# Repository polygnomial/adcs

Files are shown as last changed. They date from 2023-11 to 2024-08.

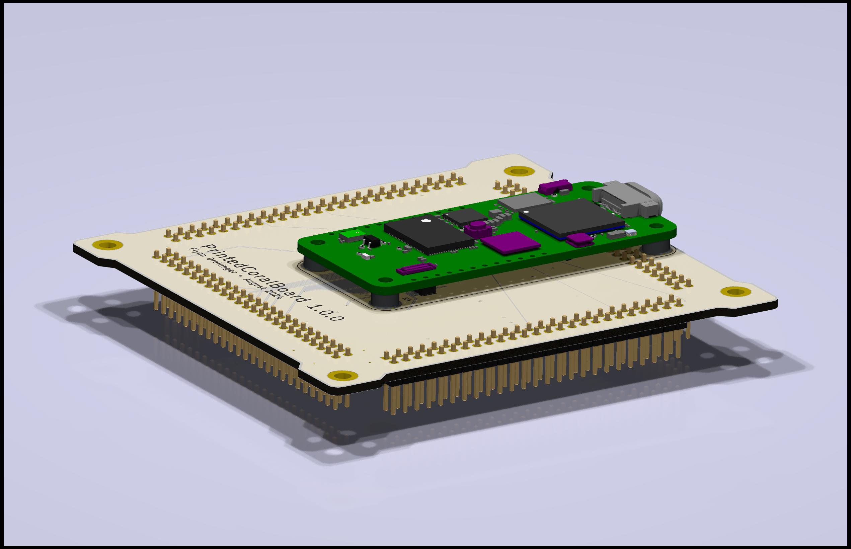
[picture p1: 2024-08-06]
hardware/coral_breakout_board/PrintedCoralBoard1.jpg

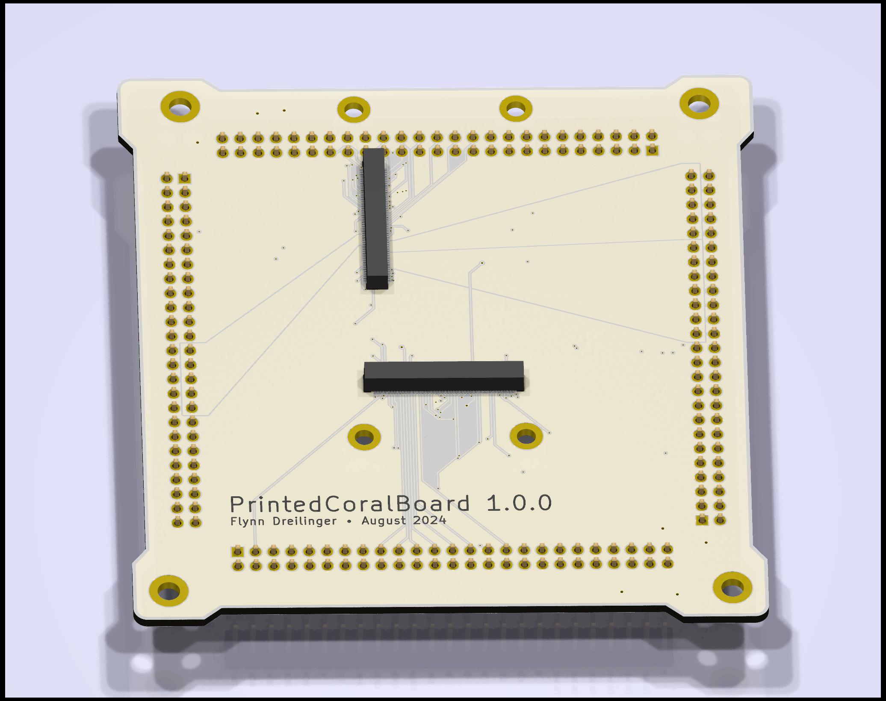
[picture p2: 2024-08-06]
hardware/coral_breakout_board/PrintedCoralBoard.jpg

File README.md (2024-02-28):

# ADCS

## Docs

- Power Architecture
- RT1170 and RT1060 pin map
- slides and other notes
- Tim's review
- TODO move other notes here

## Hardware

### Soldermander

CPU (RT1170) + RAM (MRAM - SEMC and xSPI) + power breakout board, with 2x 100-pin board to board connectors.

### Sqrt of G

Eventual functional ADCS controller and sensor mainboard that the CPU board will sit on top of

### PCBranch

Development breakout board that breaks out all the pins of the RT1170 CPU

---

## Code

### flight

Rust code with a Teensy target, RT1170 target (not yet implemented), etc.

### cpp-code

Useful for checking that I implemented my Rust drivers correctly

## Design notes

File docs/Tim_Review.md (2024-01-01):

- What is the input voltage range? Should annotate that on schematic (voltage min/max, current rating
-- added
- Inductor in line of power input?
-- done, not sure if its the best choice
- "If it's latched up, it won't be executing any code." -Pete 
	- This is not true. A latch up does not necessarily cause the CPU has crashed. In fact it generally does not, and a software protection that detects increased current and power cycles the chip is totally valid.
	- If you want to actually do this, you should do some analysis of the timing. A common way to do this is to have a capacitor on the enable pin, with a weak pull-up, and then an N-FET to ground. When you turn on the GPIO, it turns on the FET, which drains the cap really fast (nanoseconds). It take microseconds to re-charge, giving the power rails time to turn fully off, and giving the latch-up a chance to clear

- You should break out all the GPIO, even the ones the teensy does not. Just leave them as test points.
-- yeah gonna do that
- These too (the ones not going to the JTAG header):
	 ![[Pasted image 20231021010133.png|300]]
- I would add test points to the SD card interface to help debug/software
- SENSORS
	- You should have a power switch to power cycle the sensors. I would say you should put two of each sensor, and have two I2C busses, each with one of each sensor.
	- I2C isolation is not actually super practical, imo. The bus is too complicated to be able to guarantee two devices are isolated. I'd just aim for reliability by redundancy.
	-- will do both, eventually. For now, just multiple devices
	- You should break out more pins of the GPS. At least the PPS pin, which you might want to use. 
	-- added a note to schematic, not gonna do for now
	- What's the deal with this splitter thing? Why not just a splitter, or two GPS's? seems like extra points of failure on zero fault tolerant system.
	-- resolved this

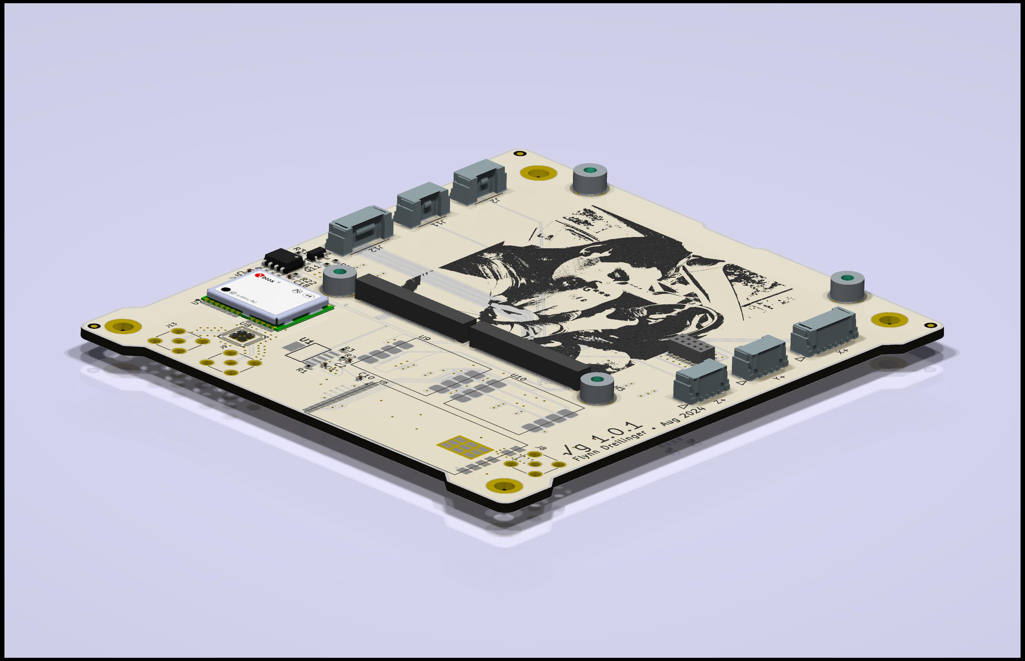
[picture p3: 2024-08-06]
hardware/adcs_with_cpu_board/sqrt_of_g_temp1.jpg

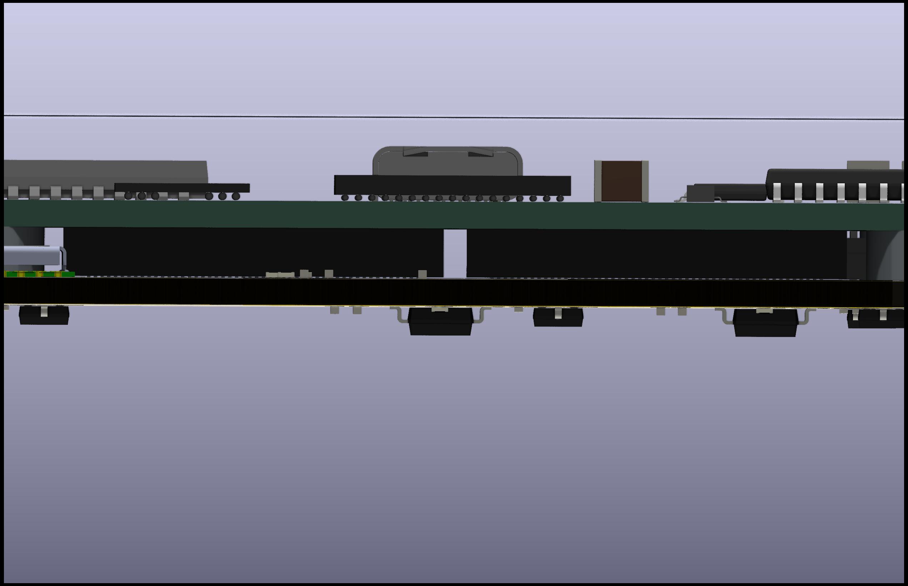
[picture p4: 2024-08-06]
hardware/adcs_with_coral/sqrt_of_g4.jpg

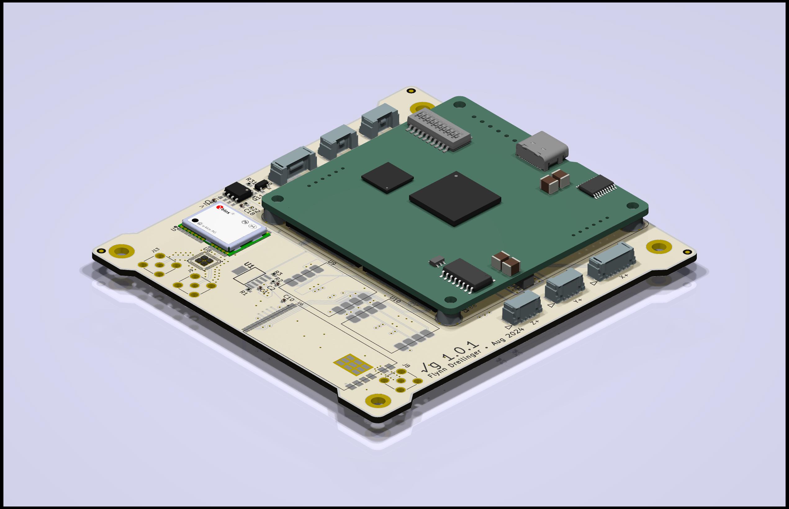
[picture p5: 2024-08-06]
hardware/adcs_with_coral/sqrt_of_g2.jpg

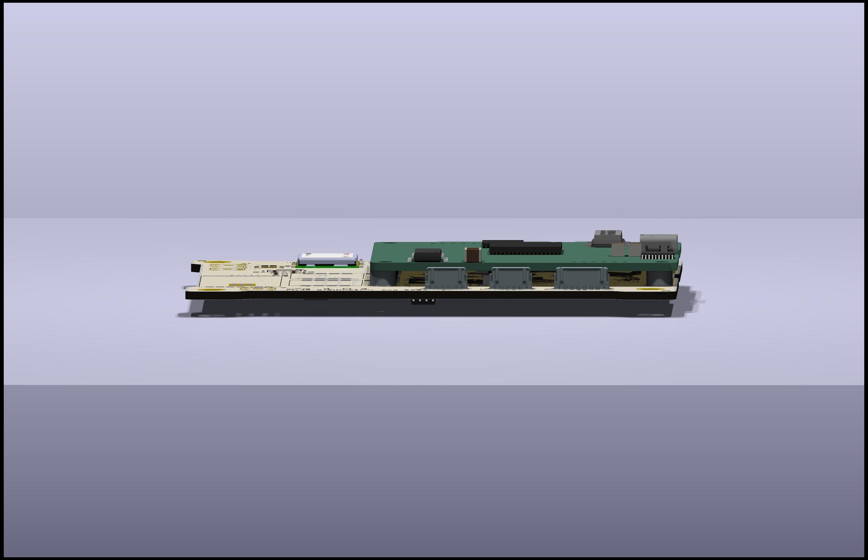
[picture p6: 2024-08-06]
hardware/adcs_with_cpu_board/sqrt_of_g3.jpg

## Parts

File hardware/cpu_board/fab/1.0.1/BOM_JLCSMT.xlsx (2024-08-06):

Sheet: Sheet1
Comment | Designator | Footprint | JLCPCB Part #（optional）
0.1uF | C10, C25, C28, C31, C34, C69, C70, C71, C72, C73, C74, C75, C84, C85 | 402
1uF | C1, C2, C3, C38, C41, C58, C59, C60, C61, C62, C63, C88, C89 | 402
4.7uF | C6, C7, C9, C23, C24, C43, C44, C51, C52, C66, C68 | 402
22uF | C4, C16, C27, C67, C76, C77, C78, C80 | 603
2.2uF | C8, C40, C45, C46, C47, C48, C49, C50 | 402
100uF | C79, C81, C82, C83 | 1210
10pF | C5, C20, C21 | 402
0.22uF | C14, C29 | 402
8pF | C18, C19 | 402
3.3nF | C86, C87 | 402
22nF | C11 | 402
47kΩ | R37, R38, R39, R40, R41, R42, R43, R44, R45, R46, R47, R48 | 402
22kΩ | R51, R52, R53, R54, R55, R56, R57, R58, R59, R60, R61, R62 | 402
10kΩ | R3, R4, R7, R12, R16, R17, R21, R33 | 402 | C3152014,
100kΩ | R8, R15, R19, R24, R31, R32, R49, R50 | 402
4.7kΩ | R9, R10, R63, R64 | 402
0Ω | R2, R26 | 402
30kΩ | R11, R34 | 402
33k | R18, R20 | 402
5.1kΩ | R22, R23 | 402
22.1kΩ | R29, R30 | 402
10mΩ | R1 | R_0402_1005Metric | C5116354
2.2MΩ | R5 | 402
1.27MΩ | R6 | 402
806kΩ | R14 | R_0402_1005Metric | C3016043
4.7K - DNP | R25 | 402
30.1kΩ | R27 | R_0402_1005Metric | C208856
73.2kΩ | R28 | 402
18kΩ | R35 | 402
3.3uH | L3, L4 | L_1210_3225Metric
330uH | L1 | IND_SRN6045TA-331K | C2049953
DLW21HN900SQ2L | L2 | IND4_CHOKE_0805 | C80529
4.7µH | L5 | IND_4x4mm | C5127393
TPS54226PWPRPWP14_2P31X2P46-L | U7, U8 | PWP14_2P31X2P46-L | C72066
TPS16630PWPR | U1 | HTSSOP20_PWP_TEX | C1849462
MIMXRT1176 | U2 | U_MIMXRT1176DVMAA_NXP | C1020268
MT29F1G01ABBFDWB | U4 | UDFN800X600X65-8 | C5330479
USBLC6-2SC6 | U5 | SOT23-6L_STM | C2687116
MT48H32M16LFB4-6 | U6 | VFBGA54_8X8_MRN | C1351581
LT3014IS5-TRMPBF | U9 | S_5_ADI | C666272
CD40109BQNSRQ1 | U10 | NS16 | C2677390
24.0mHz | Y2 | Crystal_SMD_2016-4Pin_2.0x1.6mm | C1986107
32.768kHz | Y3 | Crystal_SMD_3215-2Pin_3.2x1.5mm | C145140
SW_DIP_x10 | SW2 | SW-SMD_DSHP10TS-S | C319046
SW_DIP_x04 | SW3 | SW-SMD_8P-L6.7-W5.4-P1.27-LS8.5 | C319050
190mΩ | FB1, FB2, FB6 | Fuse_0402_1005Metric | C85812
DF40C-100DP-0.4V(51) | J6, J7 | DF40C100DP04V51 | C531031
USB_C_pycubed | J1 | USB_C_Receptacle_XKB_U262-161N-4BVC11 | C319148
JTAG_SWD_10 | J3 | PinHeader_2x05_P1.27mm_Vertical_SMD | C180221

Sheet: Sheet2
References | Value | Footprint | Description | Flight | JLCPCB P/N | Footprint (for JLCPCB) | Power Rating | Voltage Rating | Quantity
C10, C25, C28, C31, C34, C69, C70, C71, C72, C73, C74, C75, C84, C85 | 0.1uF | C_0402_1005Metric |  |  |  |  |  | 10V, 50V | 14
C1, C2, C3, C38, C41, C58, C59, C60, C61, C62, C63, C88, C89 | 1uF | C_0402_1005Metric |  |  |  | 402 |  | 50V, 10V | 13
C6, C7, C9, C23, C24, C43, C44, C51, C52, C66, C68 | 4.7uF | C_0402_1005Metric |  |  |  | 402 |  | 6.3V, 10V | 11
C4, C16, C27, C67, C76, C77, C78, C80 | 22uF | C_0603_1608Metric |  |  |  | 603 |  | 6.3V | 8
C8, C40, C45, C46, C47, C48, C49, C50 | 2.2uF | C_0402_1005Metric |  |  |  | 402 |  | 10V | 8
C79, C81, C82, C83 | 100uF | C_1210_3225Metric | 100uF 16V X5R 1210 |  |  | 1210 |  | 50V | 4
C5, C20, C21 | 10pF | C_0402_1005Metric |  |  |  | 402 |  | 50V | 3
C14, C29 | 0.22uF | C_0402_1005Metric |  |  |  | 402 |  | 50V, 6.3V | 2
C18, C19 | 8pF | C_0402_1005Metric |  |  |  | 402 |  | 50V | 2
C86, C87 | 3.3nF | C_0402_1005Metric | 3.3nF +-10% 100V X7R 0603 |  |  | 402 |  | 50V | 2
C11 | 22nF | C_0402_1005Metric |  |  |  | 402 |  | 50V | 1
R37, R38, R39, R40, R41, R42, R43, R44, R45, R46, R47, R48 | 47kΩ | R_0402_1005Metric |  |  |  | 402 |  |  | 12
R51, R52, R53, R54, R55, R56, R57, R58, R59, R60, R61, R62 | 22kΩ | R_0402_1005Metric |  |  |  | 402 |  |  | 12
R3, R4, R7, R12, R16, R17, R21, R33 | 10kΩ | R_0402_1005Metric |  |  | C3152014, | 402 |  |  | 8
R8, R15, R19, R24, R31, R32, R49, R50 | 100kΩ | R_0402_1005Metric |  |  |  | 402 |  |  | 8
R9, R10, R63, R64 | 4.7kΩ | R_0402_1005Metric |  |  |  | 402 |  |  | 4
R2, R26 | 0Ω | R_0402_1005Metric |  |  |  | 402 |  |  | 2
R11, R34 | 30kΩ | R_0402_1005Metric |  |  |  | 402 |  |  | 2
R18, R20 | 33k | R_0402_1005Metric |  |  |  | 402 |  |  | 2
R22, R23 | 5.1kΩ | R_0402_1005Metric | 5.1k 0402 |  |  | 402 |  |  | 2
R29, R30 | 22.1kΩ | R_0402_1005Metric | 22.1K 0402 |  |  | 402 |  |  | 2
R1 | 10mΩ | R_2512_6332Metric |  |  | C5116354 | 2512 | 3W |  | 1
R5 | 2.2MΩ | R_0402_1005Metric |  |  |  | 402 |  |  | 1
R6 | 1.27MΩ | R_0402_1005Metric |  |  |  | 402 |  |  | 1
R14 | 806kΩ | R_0402_1005Metric |  |  | C3016043 | 402 |  |  | 1
R25 | 4.7K - DNP | R_0402_1005Metric |  |  |  | 402 |  |  | 1
R27 | 30.1kΩ | R_0402_1005Metric | 30.1K 0402 |  | C208856 | 402 |  |  | 1
R28 | 73.2kΩ | R_0402_1005Metric | 73.2K 0402 |  |  | 402 |  |  | 1
R35 | 18kΩ | R_0402_1005Metric |  |  |  | 402 |  |  | 1
L3, L4 | 3.3uH | L_1210_3225Metric | 3.3uH Shielded Inductor | SRP3212-3R3M |  |  | 3.1A, 3.4A Saturation |  | 2
L1 | 330uH | IND_SRN6045TA-331K | Inductor | SRN6045TA-331K | C2049953 |  |  |  | 1
L2 | DLW21HN900SQ2L | IND4_CHOKE_0805 | Inductor | DLW21HN900SQ2L | C80529 |  |  |  | 1
L5 | 4.7µH | IND_4x4mm |  | SNR4030-4R7MT | C5127393 |  |  |  | 1
U7, U8 | TPS54226PWPRPWP14_2P31X2P46-L | PWP14_2P31X2P46-L | Adjustable Switching Regulator | TPS54226PWPR | C72066 |  |  |  | 2
U1 | TPS16630PWPR | HTSSOP20_PWP_TEX | Load Switch | TPS16630PWPR | C1849462 |  |  |  | 1
U2 | MIMXRT1176 | U_MIMXRT1176DVMAA_NXP | Microcontroller | MIMXRT1176AVM8A | C1020268 |  |  |  | 1
U3 | EM064LXQADG13IS1T | SON127P800X600X95-9N-D | STT-MRAM (xSPI) | EM064LXQADG13IS1T |  |  |  |  | 1
U4 | MT29F1G01ABBFDWB | UDFN800X600X65-8 | NAND Flash | MT29F1G01ABBFDWB | C5330479 |  |  |  | 1
U5 | USBLC6-2SC6 | SOT23-6L_STM | USB TVS diodes | USBLC6-2SC6 | C2687116 |  |  |  | 1
U6 | MT48H32M16LFB4-6 | VFBGA54_8X8_MRN | SDRAM | MT48H32M16LFB4-6 | C1351581 |  |  |  | 1
U9 | LT3014IS5-TRMPBF | S_5_ADI | Adjustable LDO |  | C666272 |  |  |  | 1
U10 | CD40109BQNSRQ1 | NS16 | Level Shifter |  | C2677390 |  |  |  | 1
Y2 | 24.0mHz | Crystal_SMD_2016-4Pin_2.0x1.6mm | 24.0mHz Crystal Oscillator | XRCGB24M000F1H01R0 | C1986107 |  |  |  | 1
Y3 | 32.768kHz | Crystal_SMD_3215-2Pin_3.2x1.5mm | 32.768kHz Crystal Oscillator | 20021221-00010C4LF | C145140 |  |  |  | 1
SW1 | SWITCH_SMT4.6X2.8 | BTN_KMR2_4.6X2.8 |  |  |  |  |  |  | 1
SW2 | SW_DIP_x10 | SW-SMD_DSHP10TS-S |  |  | C319046 |  |  |  | 1
SW3 | SW_DIP_x04 | SW-SMD_8P-L6.7-W5.4-P1.27-LS8.5 |  |  | C319050 |  |  |  | 1
FB1, FB2, FB6 | 190mΩ | Fuse_0402_1005Metric | Ferrite Bead | BLM15AG121SN1D | C85812 | 401 |  |  | 3
H2, H3, H4 | MountingHole_Pad | MountingHole_2.7mm_M2.5_DIN965_Pad |  |  |  |  |  |  | 3
J2, J4 | 353620650 | MOLEX_35362-0650 | 6-pin sherlock through-hole connector | 353620650 |  |  |  |  | 2
J6, J7 | DF40C-100DP-0.4V(51) | DF40C100DP04V51 | Hirose Board-to-Board Connector | DF40C-100DP-0.4V(51) | C531031 |  |  |  | 2
J1 | USB_C_pycubed | USB_C_Receptacle_XKB_U262-161N-4BVC11 | USB C Receptacle | U262-161N-4BVC11 | C319148 |  |  |  | 1
J3 | JTAG_SWD_10 | PinHeader_2x05_P1.27mm_Vertical_SMD | JTAG/SWD 10-pin connector | BD125-10-A-0305-0580-L-B | C180221 |  |  |  | 1
J5 | Conn_01x06 | PinHeader_1x06_P2.54mm_Vertical |  |  |  |  |  |  | 1
J8 | SAMTEC-FTS-105-03-X-DV | SAMTEC-FTS-105-03-X-DV |  |  |  |  |  |  | 1

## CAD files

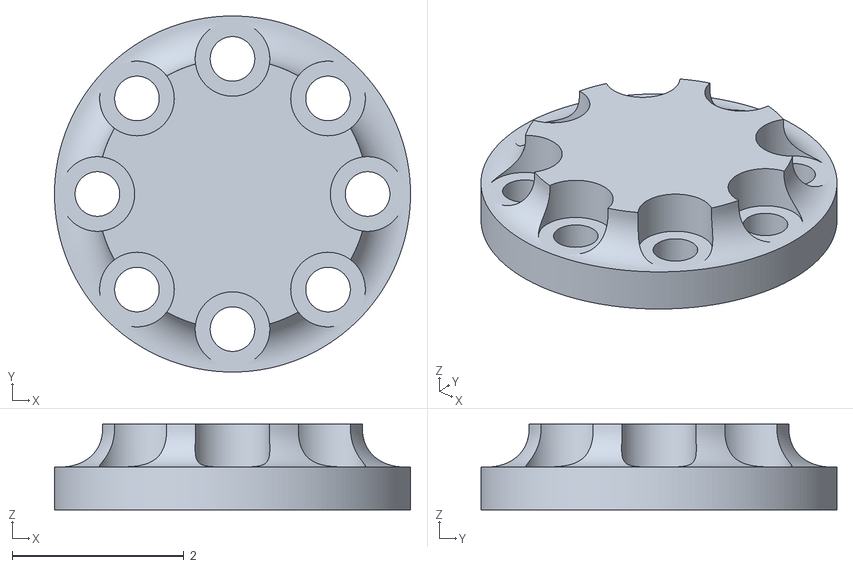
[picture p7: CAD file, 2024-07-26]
calibration/flange_test_mount.stl
4.15 x 4.15 x 1.00

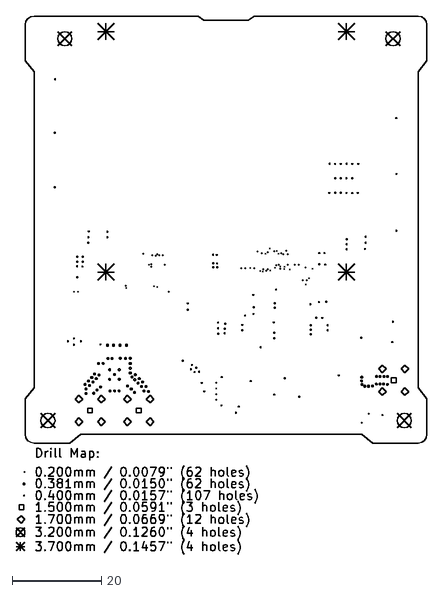
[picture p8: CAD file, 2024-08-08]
hardware/adcs_with_coral/fab/sqrt_of_g-PTH-drl_map.dxf
92.2 x 120.8

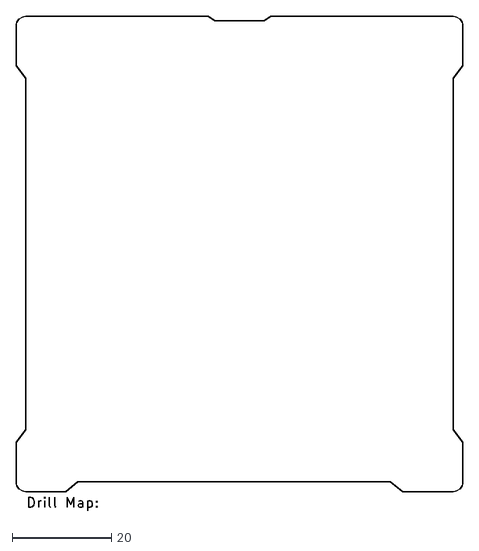
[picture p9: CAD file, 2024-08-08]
hardware/adcs_with_cpu_board/fab/sqrt_of_g-NPTH-drl_map.dxf
90.2 x 99.7

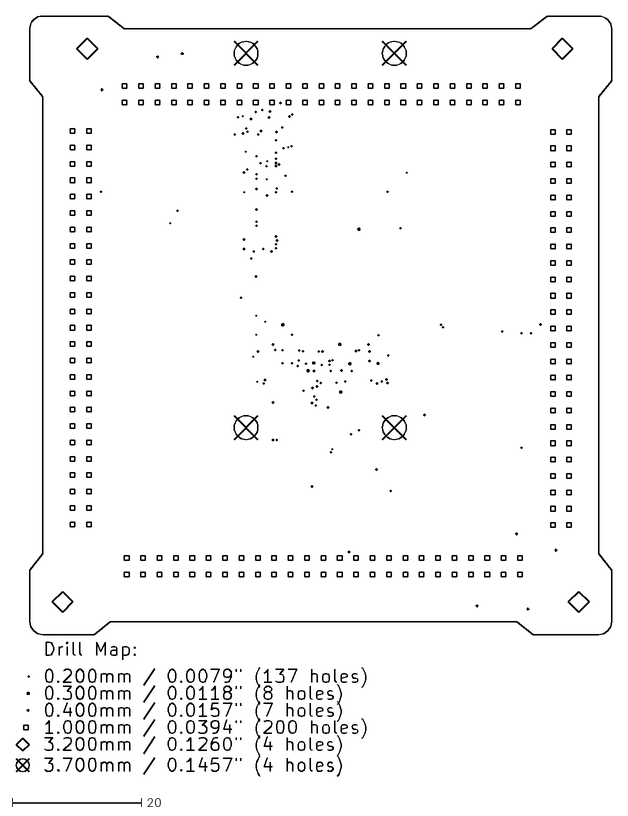
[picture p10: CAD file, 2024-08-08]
hardware/coral_breakout_board/fab/PrintedCoralBoard-PTH-drl_map.dxf
92.2 x 117.8

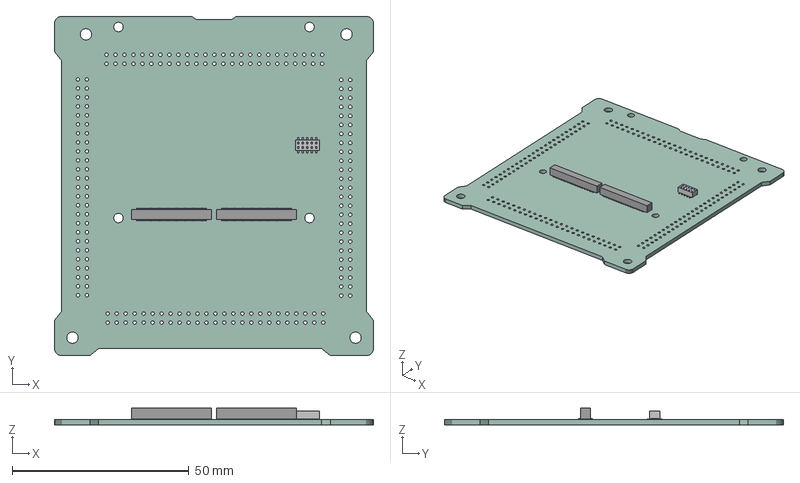
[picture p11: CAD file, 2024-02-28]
hardware/coral_breakout_board/PrintedCoralBoard.step
90.2 x 95.9 x 4.78 mm
_autosave-PCBranch PCB

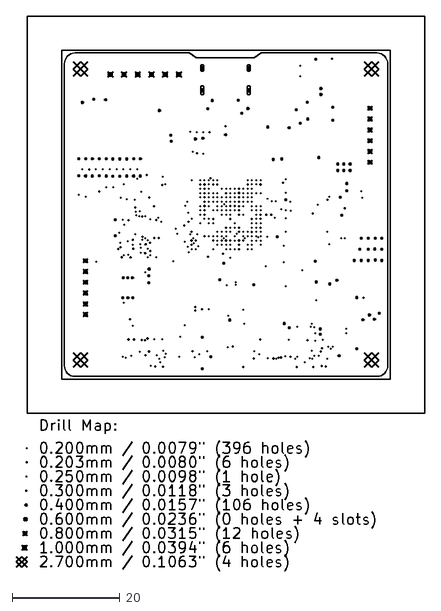
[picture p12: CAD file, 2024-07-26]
hardware/cpu_board/fab/1.0.1/Soldermander_panelized_panelized-PTH-drl_map.dxf
75.8 x 103.0

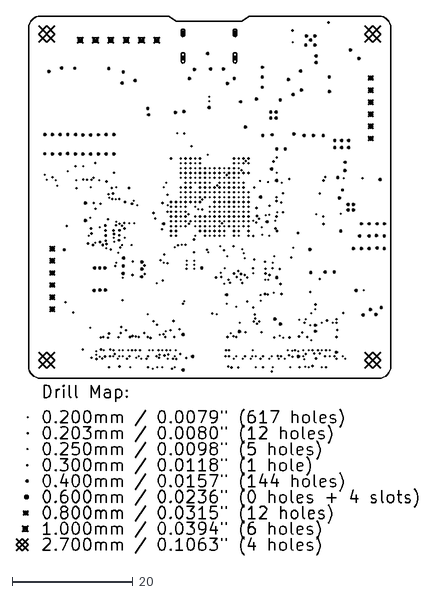
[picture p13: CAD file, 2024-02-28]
hardware/cpu_board/fab/1.0/cpu_board-PTH-drl_map.dxf
66.5 x 89.3

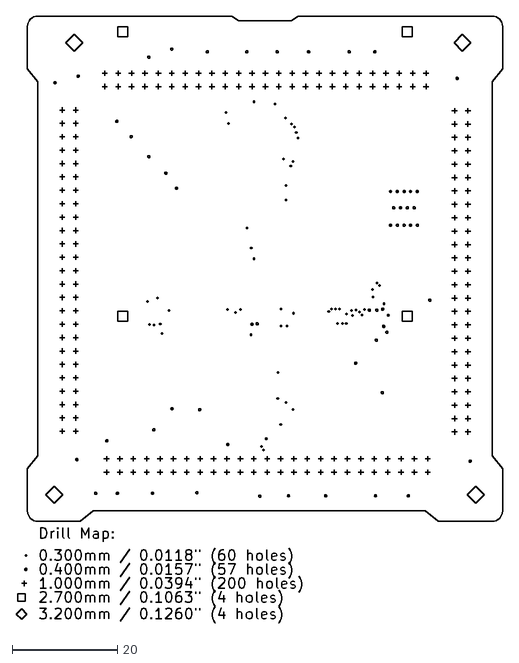
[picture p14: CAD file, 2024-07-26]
hardware/cpu_board_breakout/fab/1.0.1/PCBranch-PTH-drl_map.dxf
92.2 x 115.2

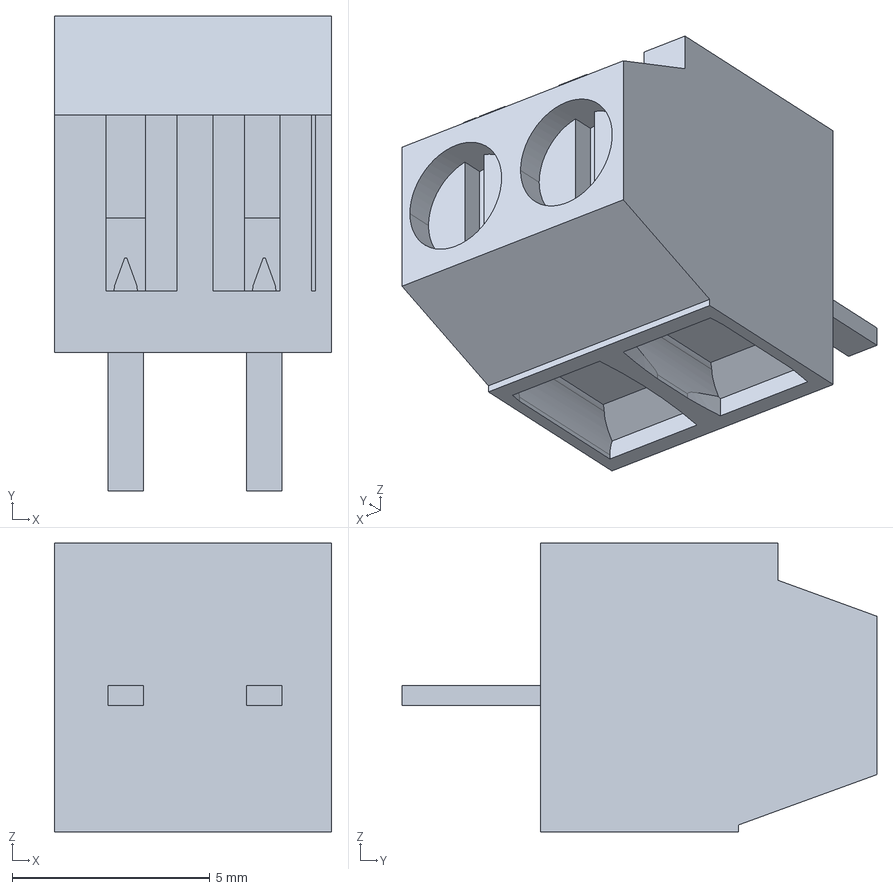
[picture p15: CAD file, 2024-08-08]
hardware/models/c-1776112-2-o-3d.stp
7.00 x 12.0 x 7.30 mm

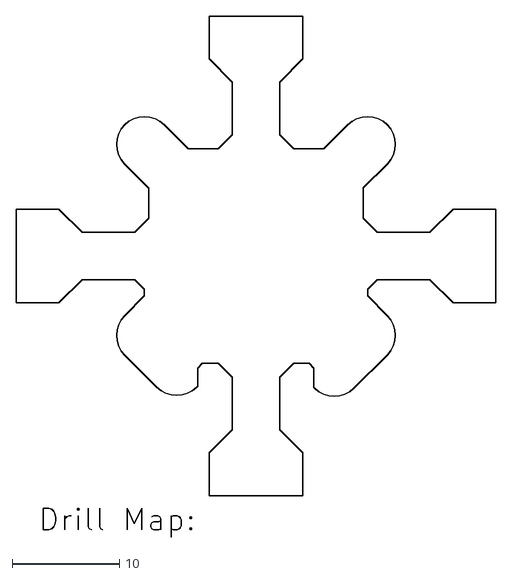
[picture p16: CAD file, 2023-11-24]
hardware/sun_sensor_pyramid/gerbers/sfh2430_breakout-NPTH-drl_map.dxf
44.7 x 48.6

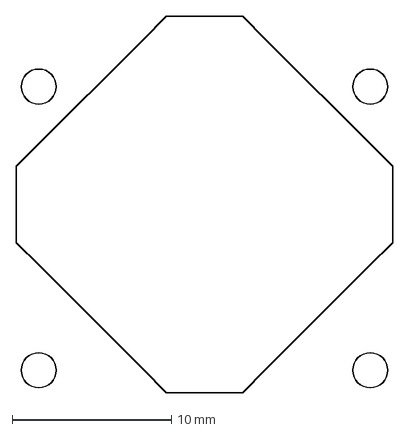
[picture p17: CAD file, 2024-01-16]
hardware/sun_sensor_pyramid/sun pyramid mounting.dxf
23.6 x 23.6 mm

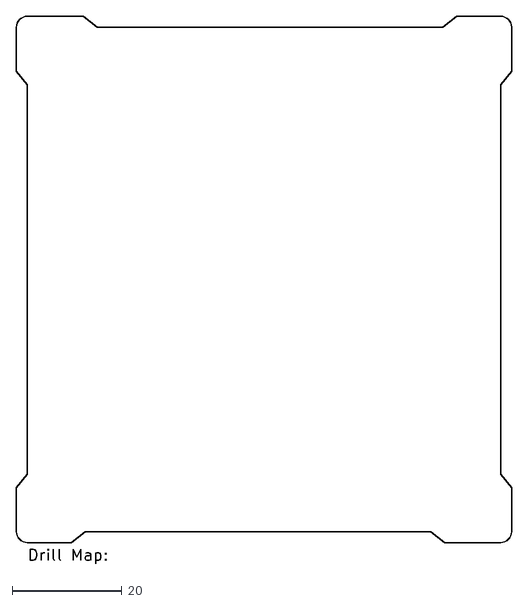
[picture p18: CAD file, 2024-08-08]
hardware/coral_breakout_board/fab/PrintedCoralBoard-NPTH-drl_map.dxf
90.2 x 99.7

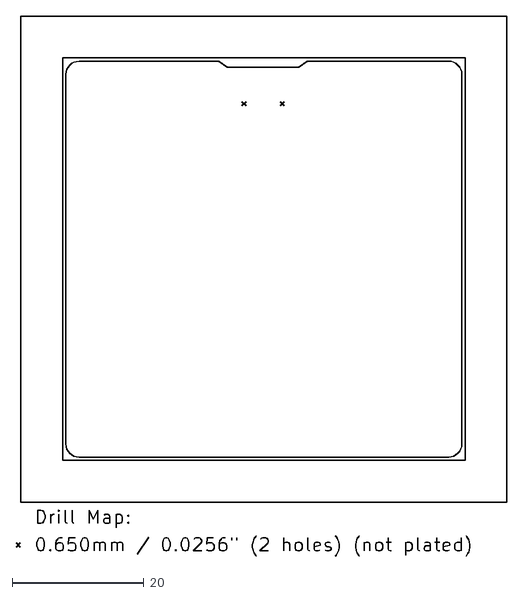
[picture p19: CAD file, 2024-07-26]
hardware/cpu_board/fab/1.0.1/Soldermander_panelized_panelized-NPTH-drl_map.dxf
74.4 x 81.8

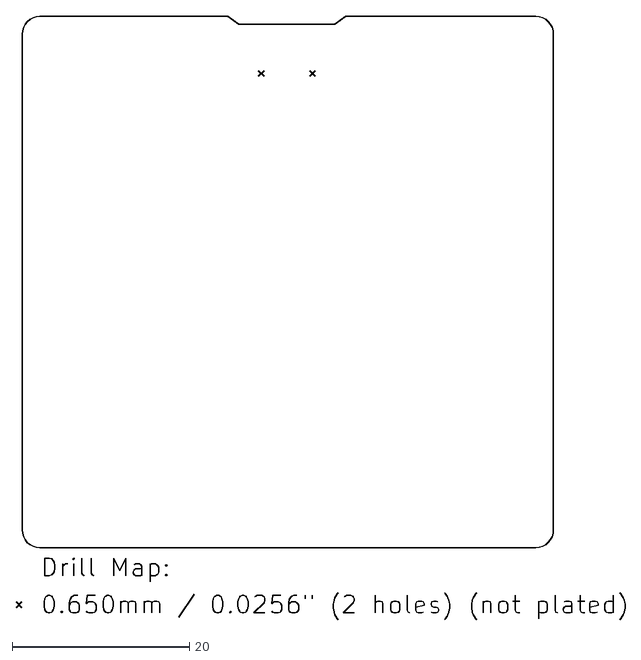
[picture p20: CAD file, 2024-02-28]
hardware/cpu_board/fab/1.0/cpu_board-NPTH-drl_map.dxf
68.8 x 68.1

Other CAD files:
hardware/cpu_board_breakout/fab/1.0.1/PCBranch-NPTH-drl_map.dxf
hardware/models/10DIP.step
hardware/models/2053380006.stp
hardware/models/35362-0850.stp
hardware/models/353621050.stp
hardware/models/5055670631.stp
hardware/models/5055680431.stp
hardware/models/5055680631.stp
hardware/models/9774030151R.stp
hardware/models/BMI270.step
hardware/models/CLP-105-02-F-D.stp
hardware/models/CONN_PH1RB-06.step
hardware/models/DF40HC_3.0_-100DS-0.4V_51_.stp
hardware/models/DRV8332DKDR.stp
hardware/models/EM064LXOAB320IS1T.stp
hardware/models/EM064LXQADG13IS1T.stp
hardware/models/FTS-105-03-F-DV.stp
hardware/models/MIMXRT1062DVJ6B.step
hardware/models/MT29F2G01ABBGDWB-IT_G_TR.stp
hardware/models/NEO.STEP
hardware/models/NS0016A.stp
hardware/models/PWP0020T.stp
hardware/models/RFM95W-915S2.step
hardware/models/SFH_2430-Z.step
hardware/models/SMA-J-P-H-ST-EM1--3DModel-STEP-269445.STEP
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

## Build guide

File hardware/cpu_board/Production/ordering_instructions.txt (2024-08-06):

Ordering Instructions:
Panel dimensions: 73.70 x 73.71 mm.
Solder Mask: Red (Default)
Silkscreen: White (Default)
Layers: 6
Finish: HASL Lead-free (Default)
Thickness: 1.6mm (Default)
Copper weight: 1oz (Default)
Minimum track width: 0.09mm (3.54mil)
Minimum via drill: 0.20mm (7.87mil)

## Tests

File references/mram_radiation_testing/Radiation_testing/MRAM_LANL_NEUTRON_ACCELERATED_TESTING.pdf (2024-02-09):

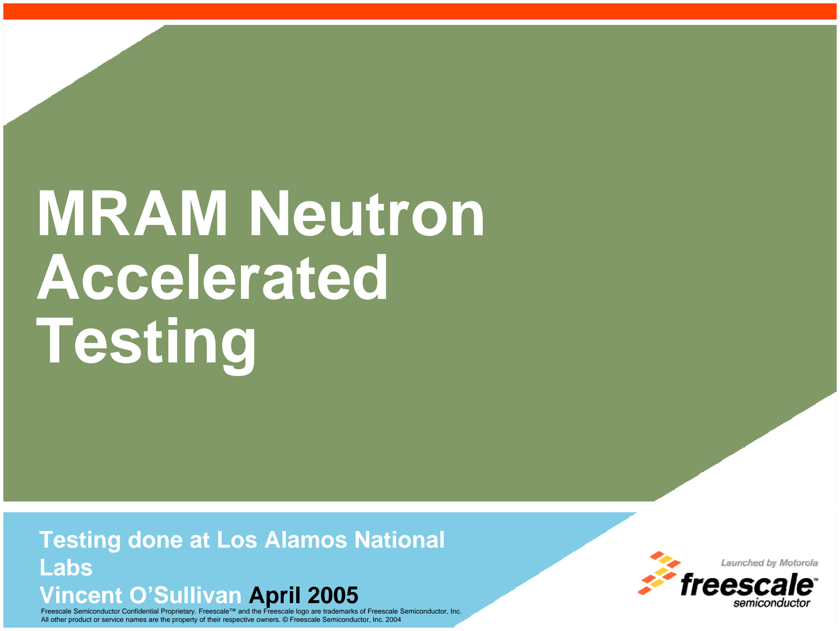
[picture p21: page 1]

Freescale Semiconductor Confidential Proprietary. Freescale™ and the Freescale logo are trademarks of Freescale Semiconductor, Inc. All other product or service names are the property of their respective owners. © Freescale Semiconductor, Inc. 2004

# MRAM Neutron Accelerated Testing

# Testing done at Los Alamos National Labs Vincent O’Sullivan April 2005

## Slide 2

# LANL Neutron Beam Overview

# LANL Neutron Beam at WNR Facilty

# - Intensity: 100M x Ambient Neutron Flux at Sea Level New York City - Energy Spectrum: Approx 1Mev to 800Mev per neutron - Spectrum is close to Ambient Neutron flux from Sea level up to commercial aircraft altitudes

# Ambient Neutron Spectrum vs WNR Spectrum

# Comparison of Neutron Flux at Ground Level and in WNR beam

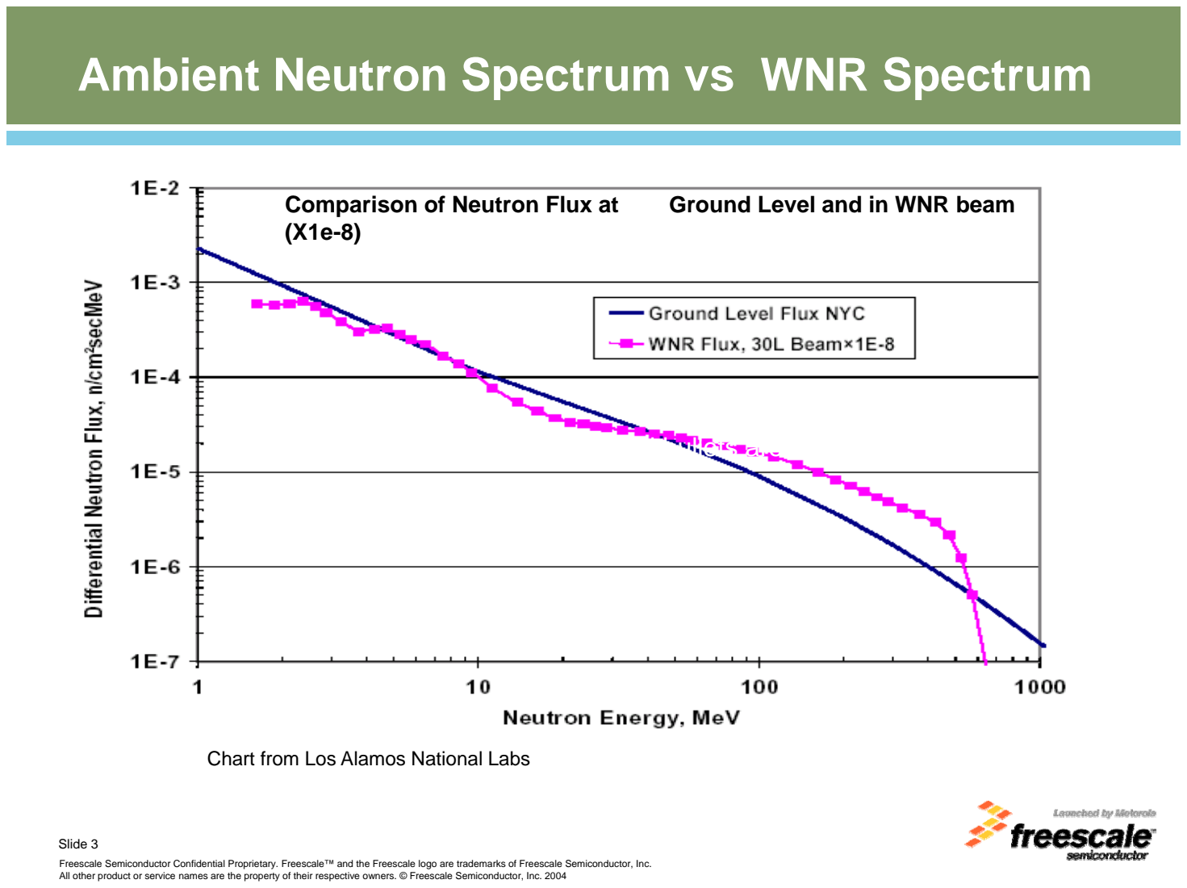
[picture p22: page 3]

## Slide 3

(X1e-8)

# ▪Third and fourth-level bullets are 16 pt Arial

# Chart from Los Alamos National Labs

## Slide 4

# Test Procedure

- Write 8 devices with all ones and 8 devices with all zeroes.

# - Expose sets of 4 devices with both data states to significantly different doses of neutrons

- Maintain 1 set of 4 with both data states as controls.

# - Capture bit fail before and after beam exposure

# - Used devices from Lot T38838

## Slide 5

# Data Summary

Run | | Total Neutrons/cm2 >10Mev | Equivalent Device Hours in NYC | Total bit fails Pre | Total Bit Fails Post
0 | Set 0 | 0 | | 37 | 40
1.0 | Set 1 | 853075578.5 | 60933969.89 | 11 | 3
2.0 | Set 2 | 851959966.4 | 60854283.32 | 8 | 6
3.0 | Set 3
4.0 | Set 3
5.0 | Set 3 | 14142335140 | 1010166796 | 4 | 3
6.0 | Set 4
7.0 | Set 4
8.0 | Set 4
8.1 | Set 4
9.0 | Set 4
10.0 | Set 4
11.0 | Set 4 | 58341176078 | 4167226863 | 0 | 1

# Neutrons are apparently good for MRAM! Worst case

provides a FIT rate of no higher than 4.2. Number of fails,

# however, are too small, and within inherent non

repeatability of setup.

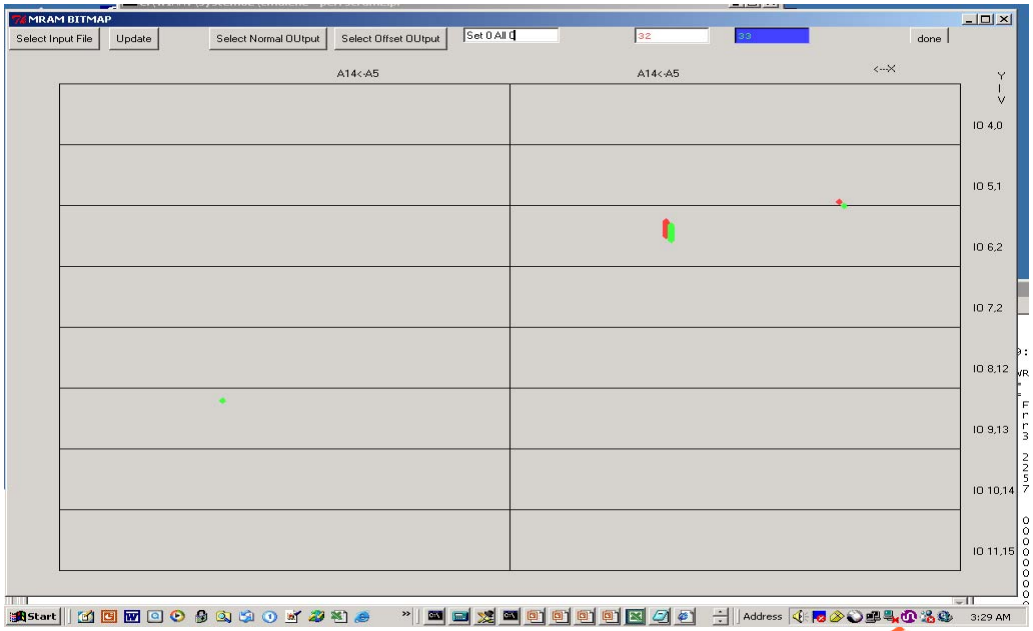
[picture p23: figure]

## Slide 6

# Set0 All 0 Pre Post

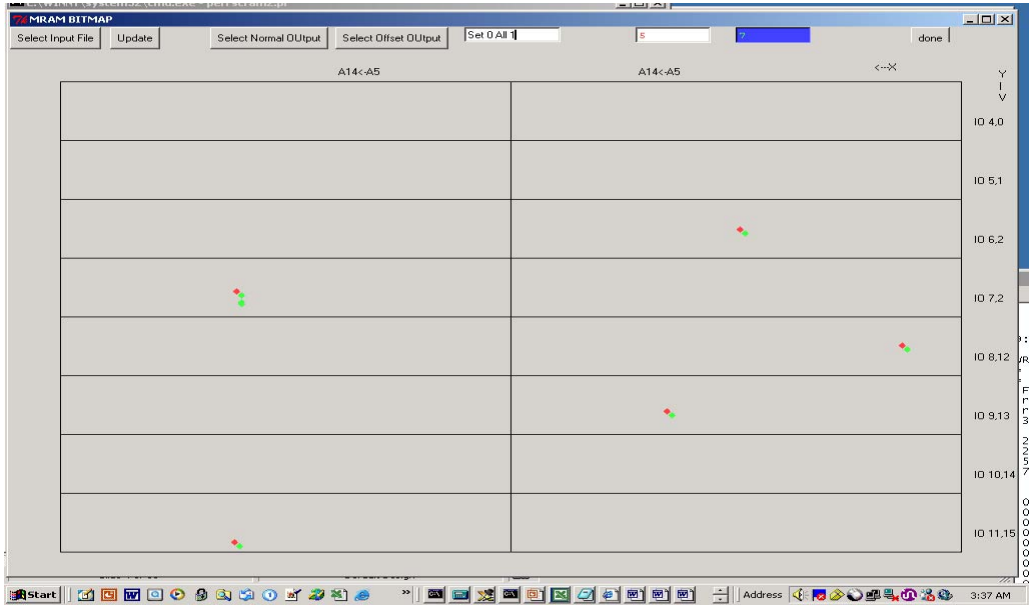
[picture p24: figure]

## Slide 7

# Set0 All 1 Pre Post

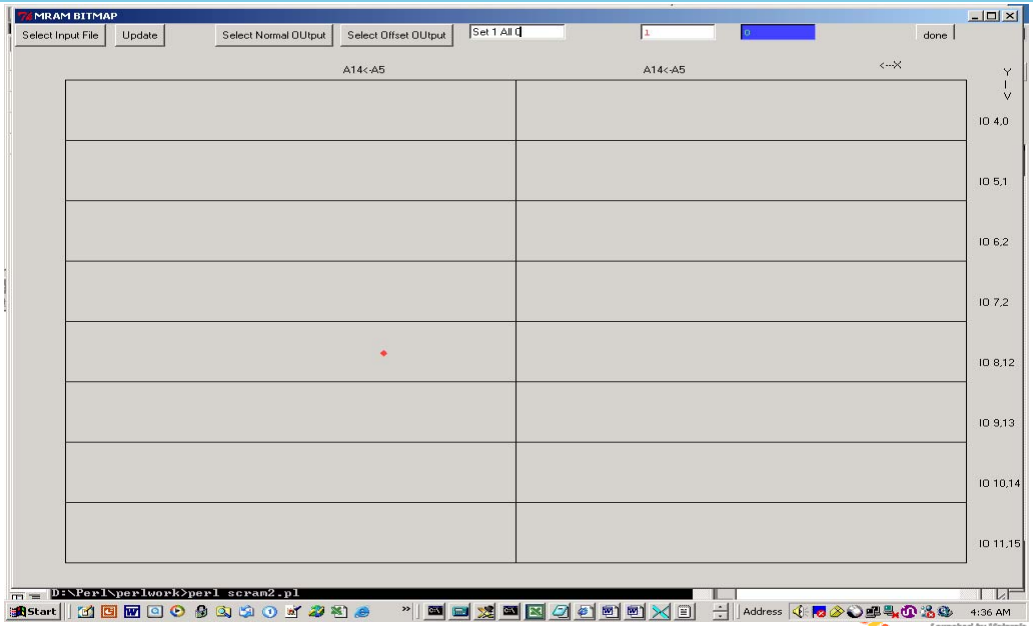
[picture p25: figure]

## Slide 8

# Set1 All 0 Pre Post

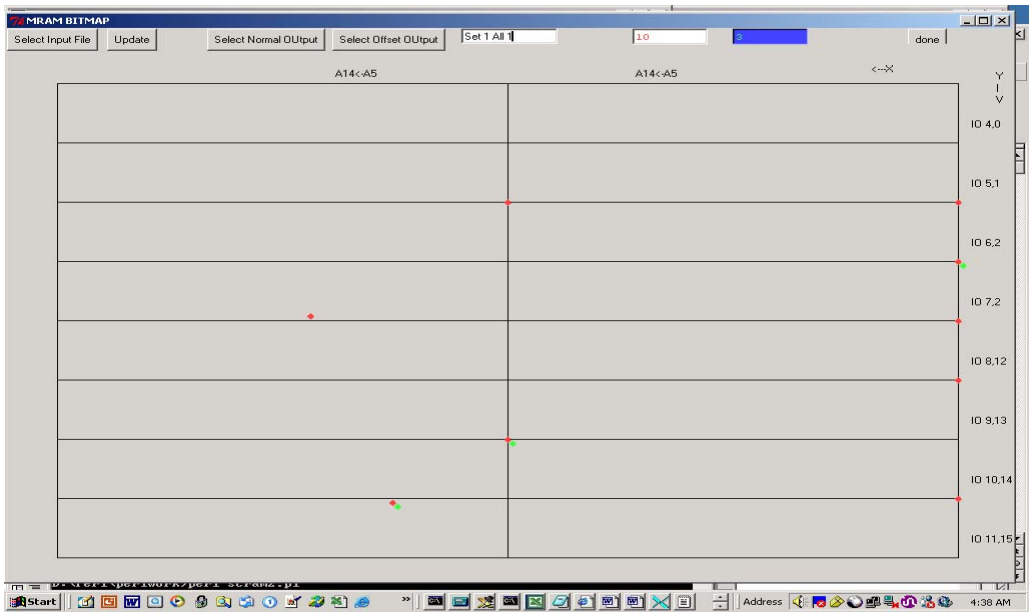
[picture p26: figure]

## Slide 9

# Set1 All 1 Pre Post

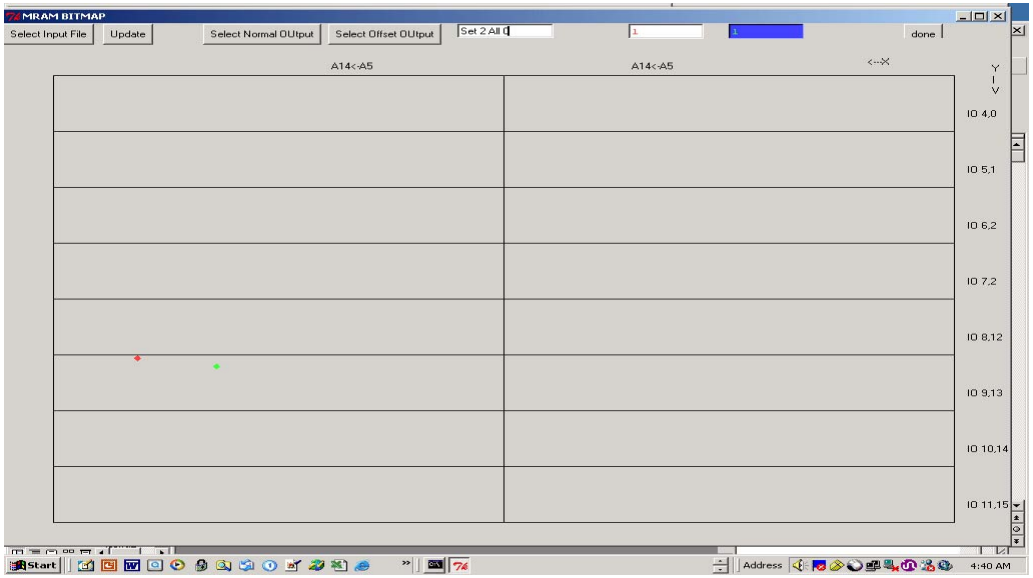
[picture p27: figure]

## Slide 10

# Set 2 All 0 Pre Post

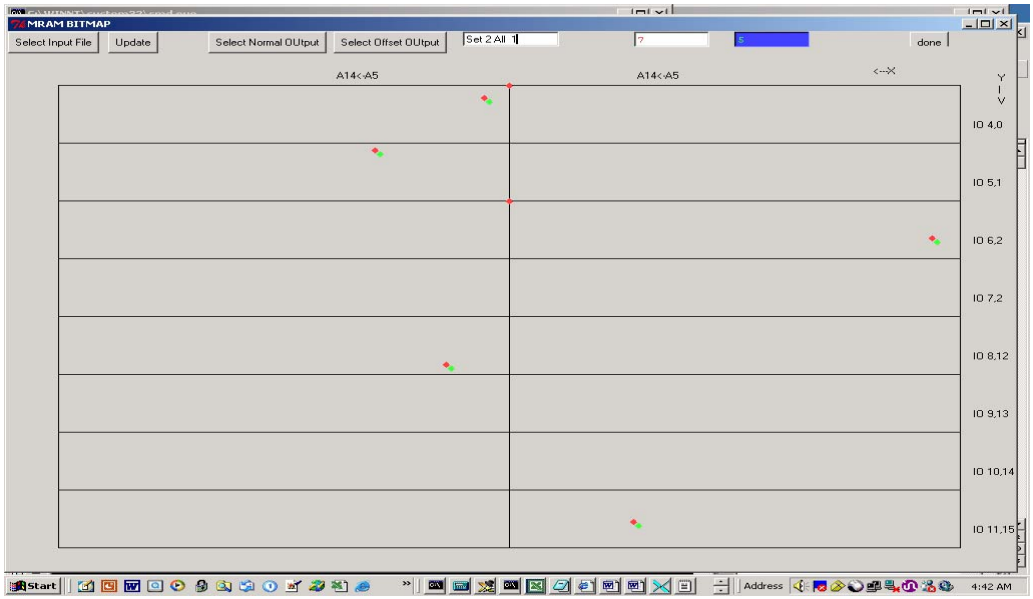
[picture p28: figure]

## Slide 11

# Set 2 All 1 Pre Post

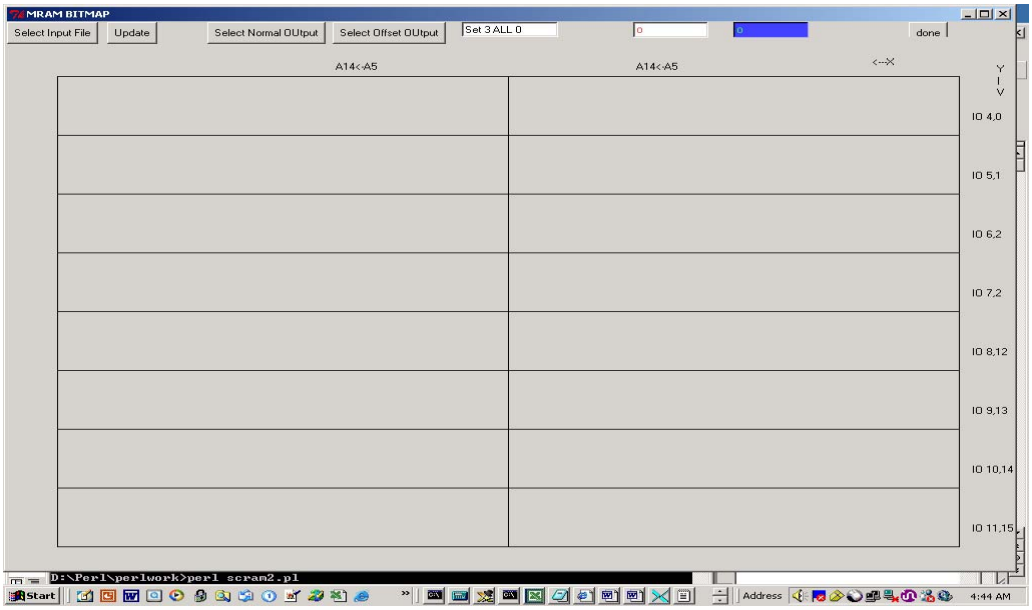
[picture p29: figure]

## Slide 12

# Set 3 All 0 Pre Post

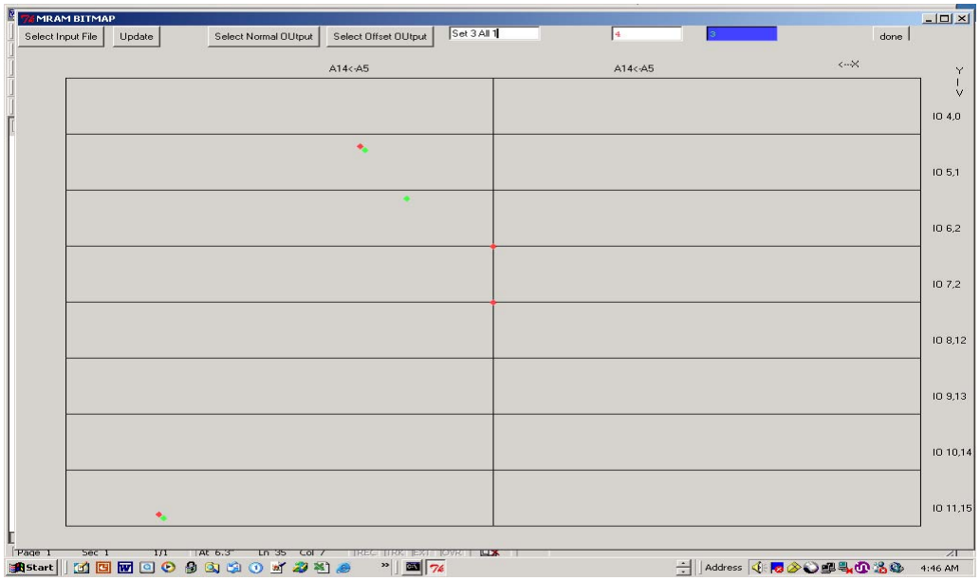
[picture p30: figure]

## Slide 13

# Set 3 All 1 Pre Post


## Slide 14

# Set 4 All 0 Pre Post


## Slide 15

# Set 4 All 1 Pre Post

## Slide 16

# Conclusions

# - MRAM Static SER FIT rate due to neutrons is likely 100’s X less than the latest SRAM technologies - To Do:

# - Characterize dynamic MRAM neutron accelerated SER - If MRAM bitcell proves as robust as expected against neutron accelerated soft error, it may be used to characterize transistor technologies in periphery against neutron accelerated dynamic SER

- MRAM Alpha accelerated soft error needs verification.


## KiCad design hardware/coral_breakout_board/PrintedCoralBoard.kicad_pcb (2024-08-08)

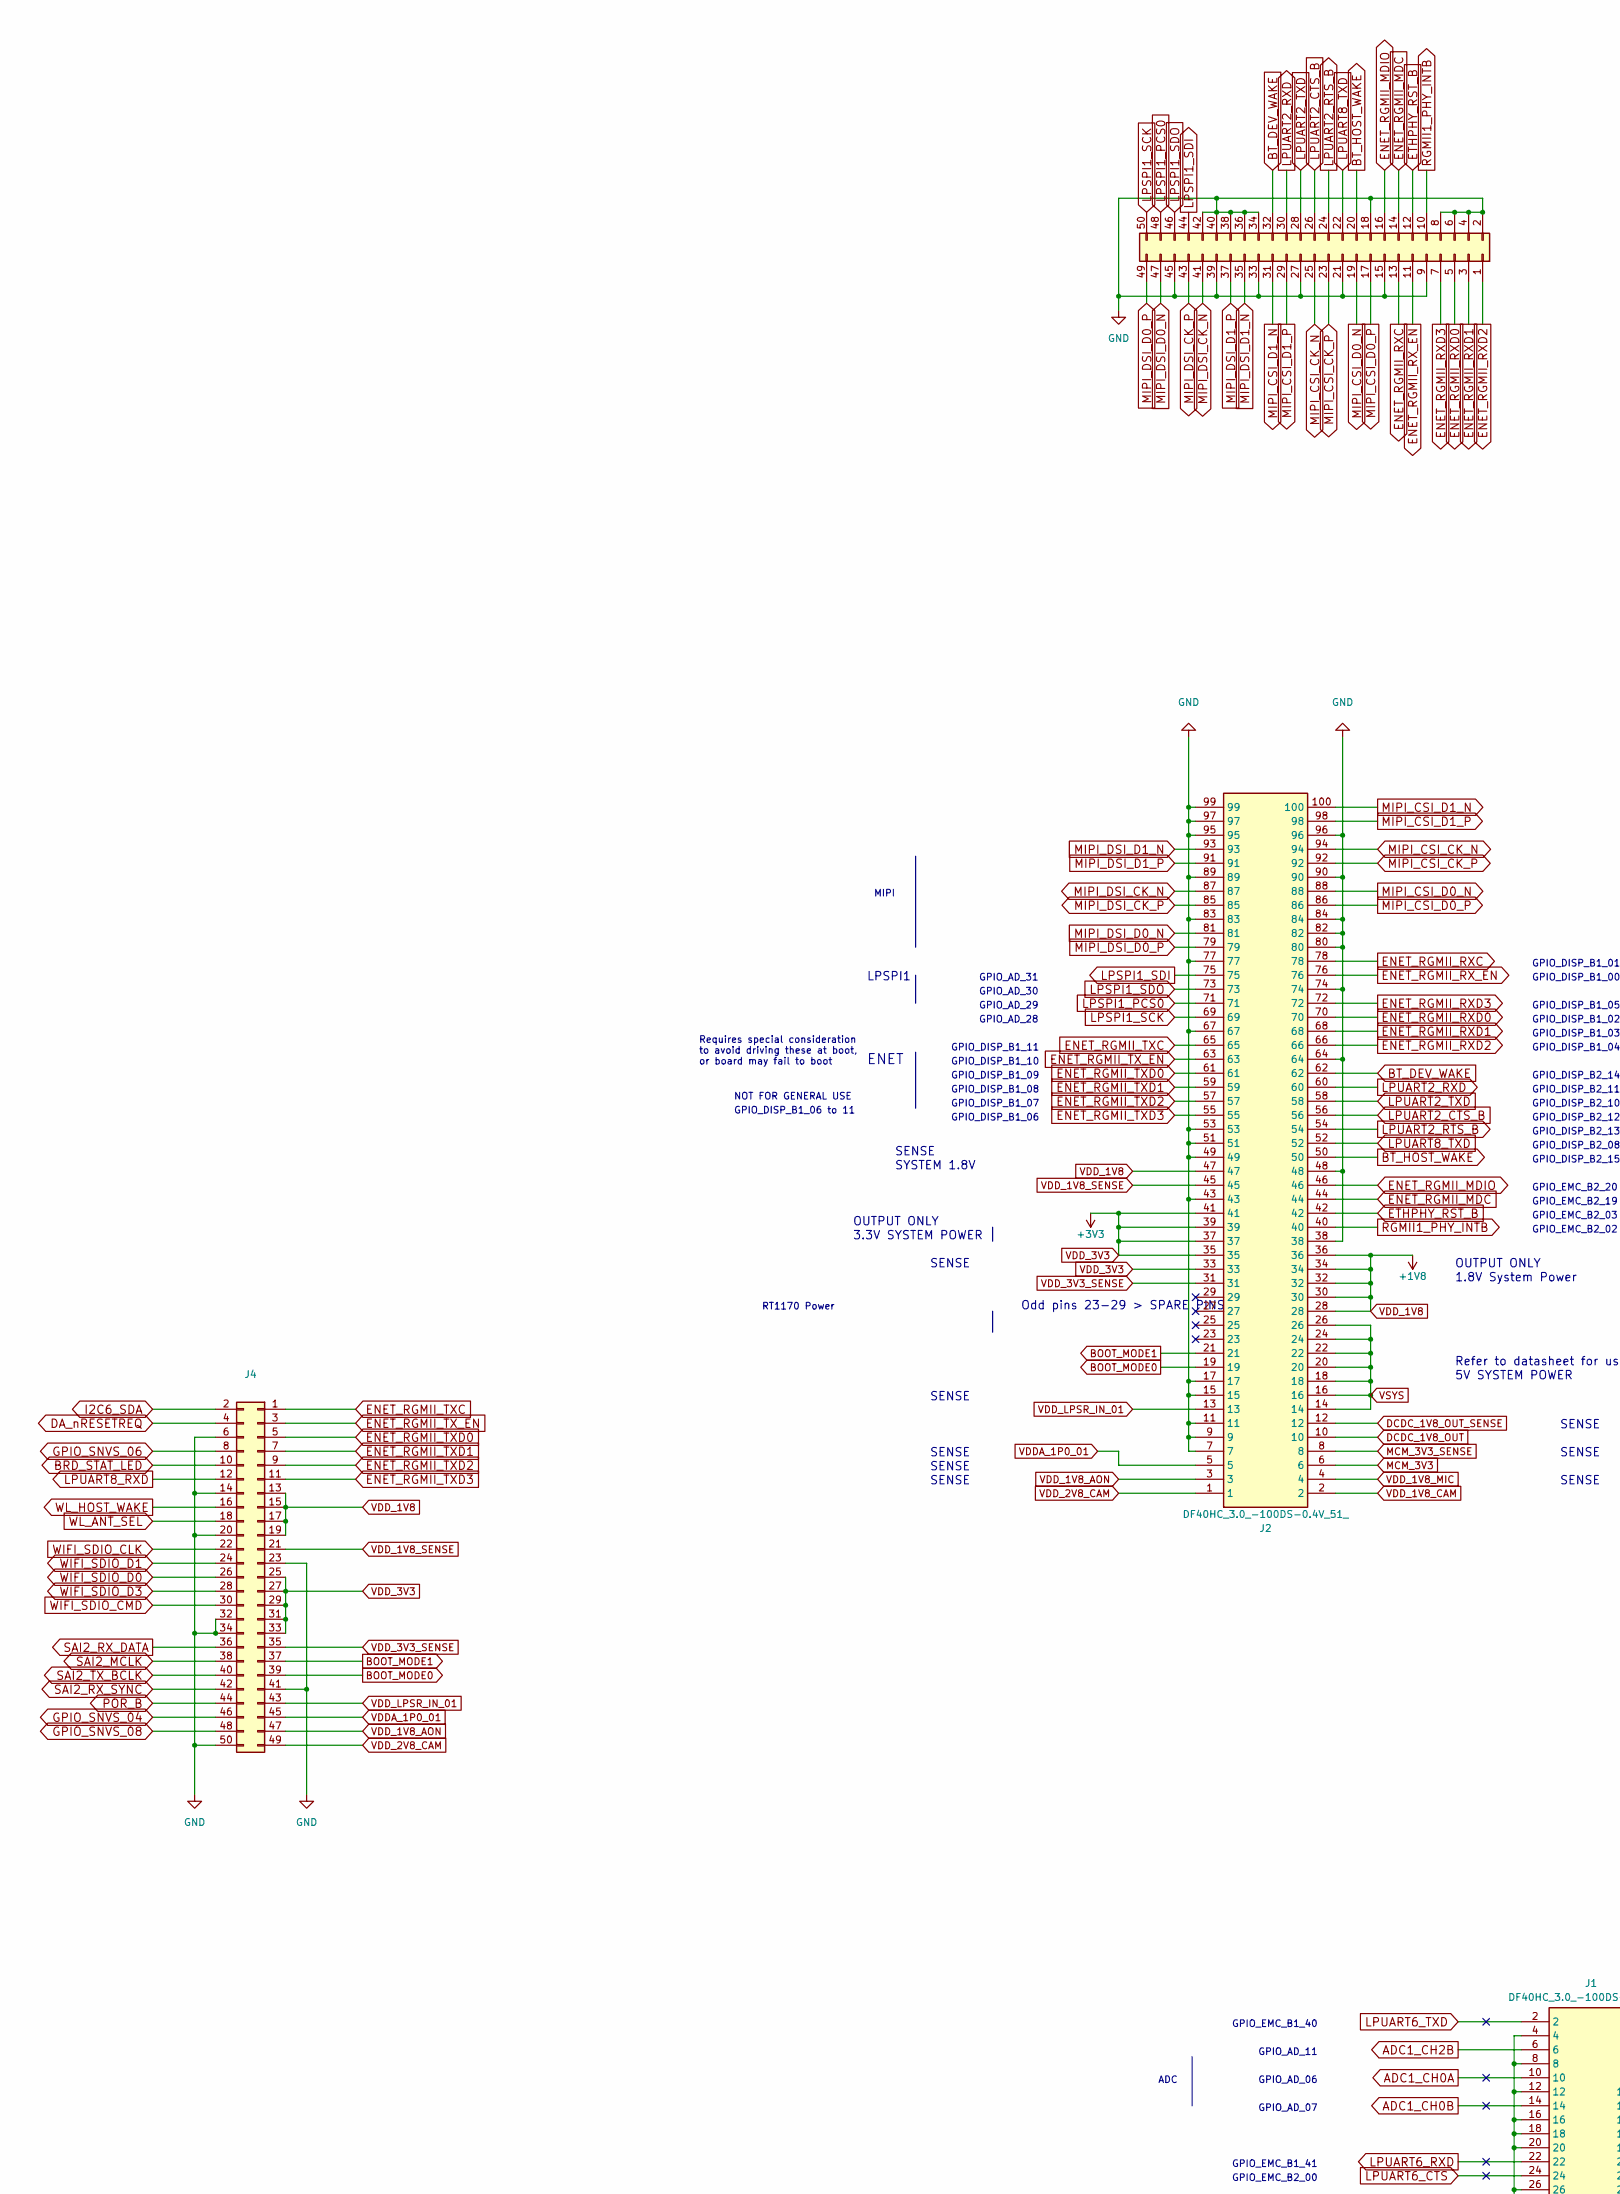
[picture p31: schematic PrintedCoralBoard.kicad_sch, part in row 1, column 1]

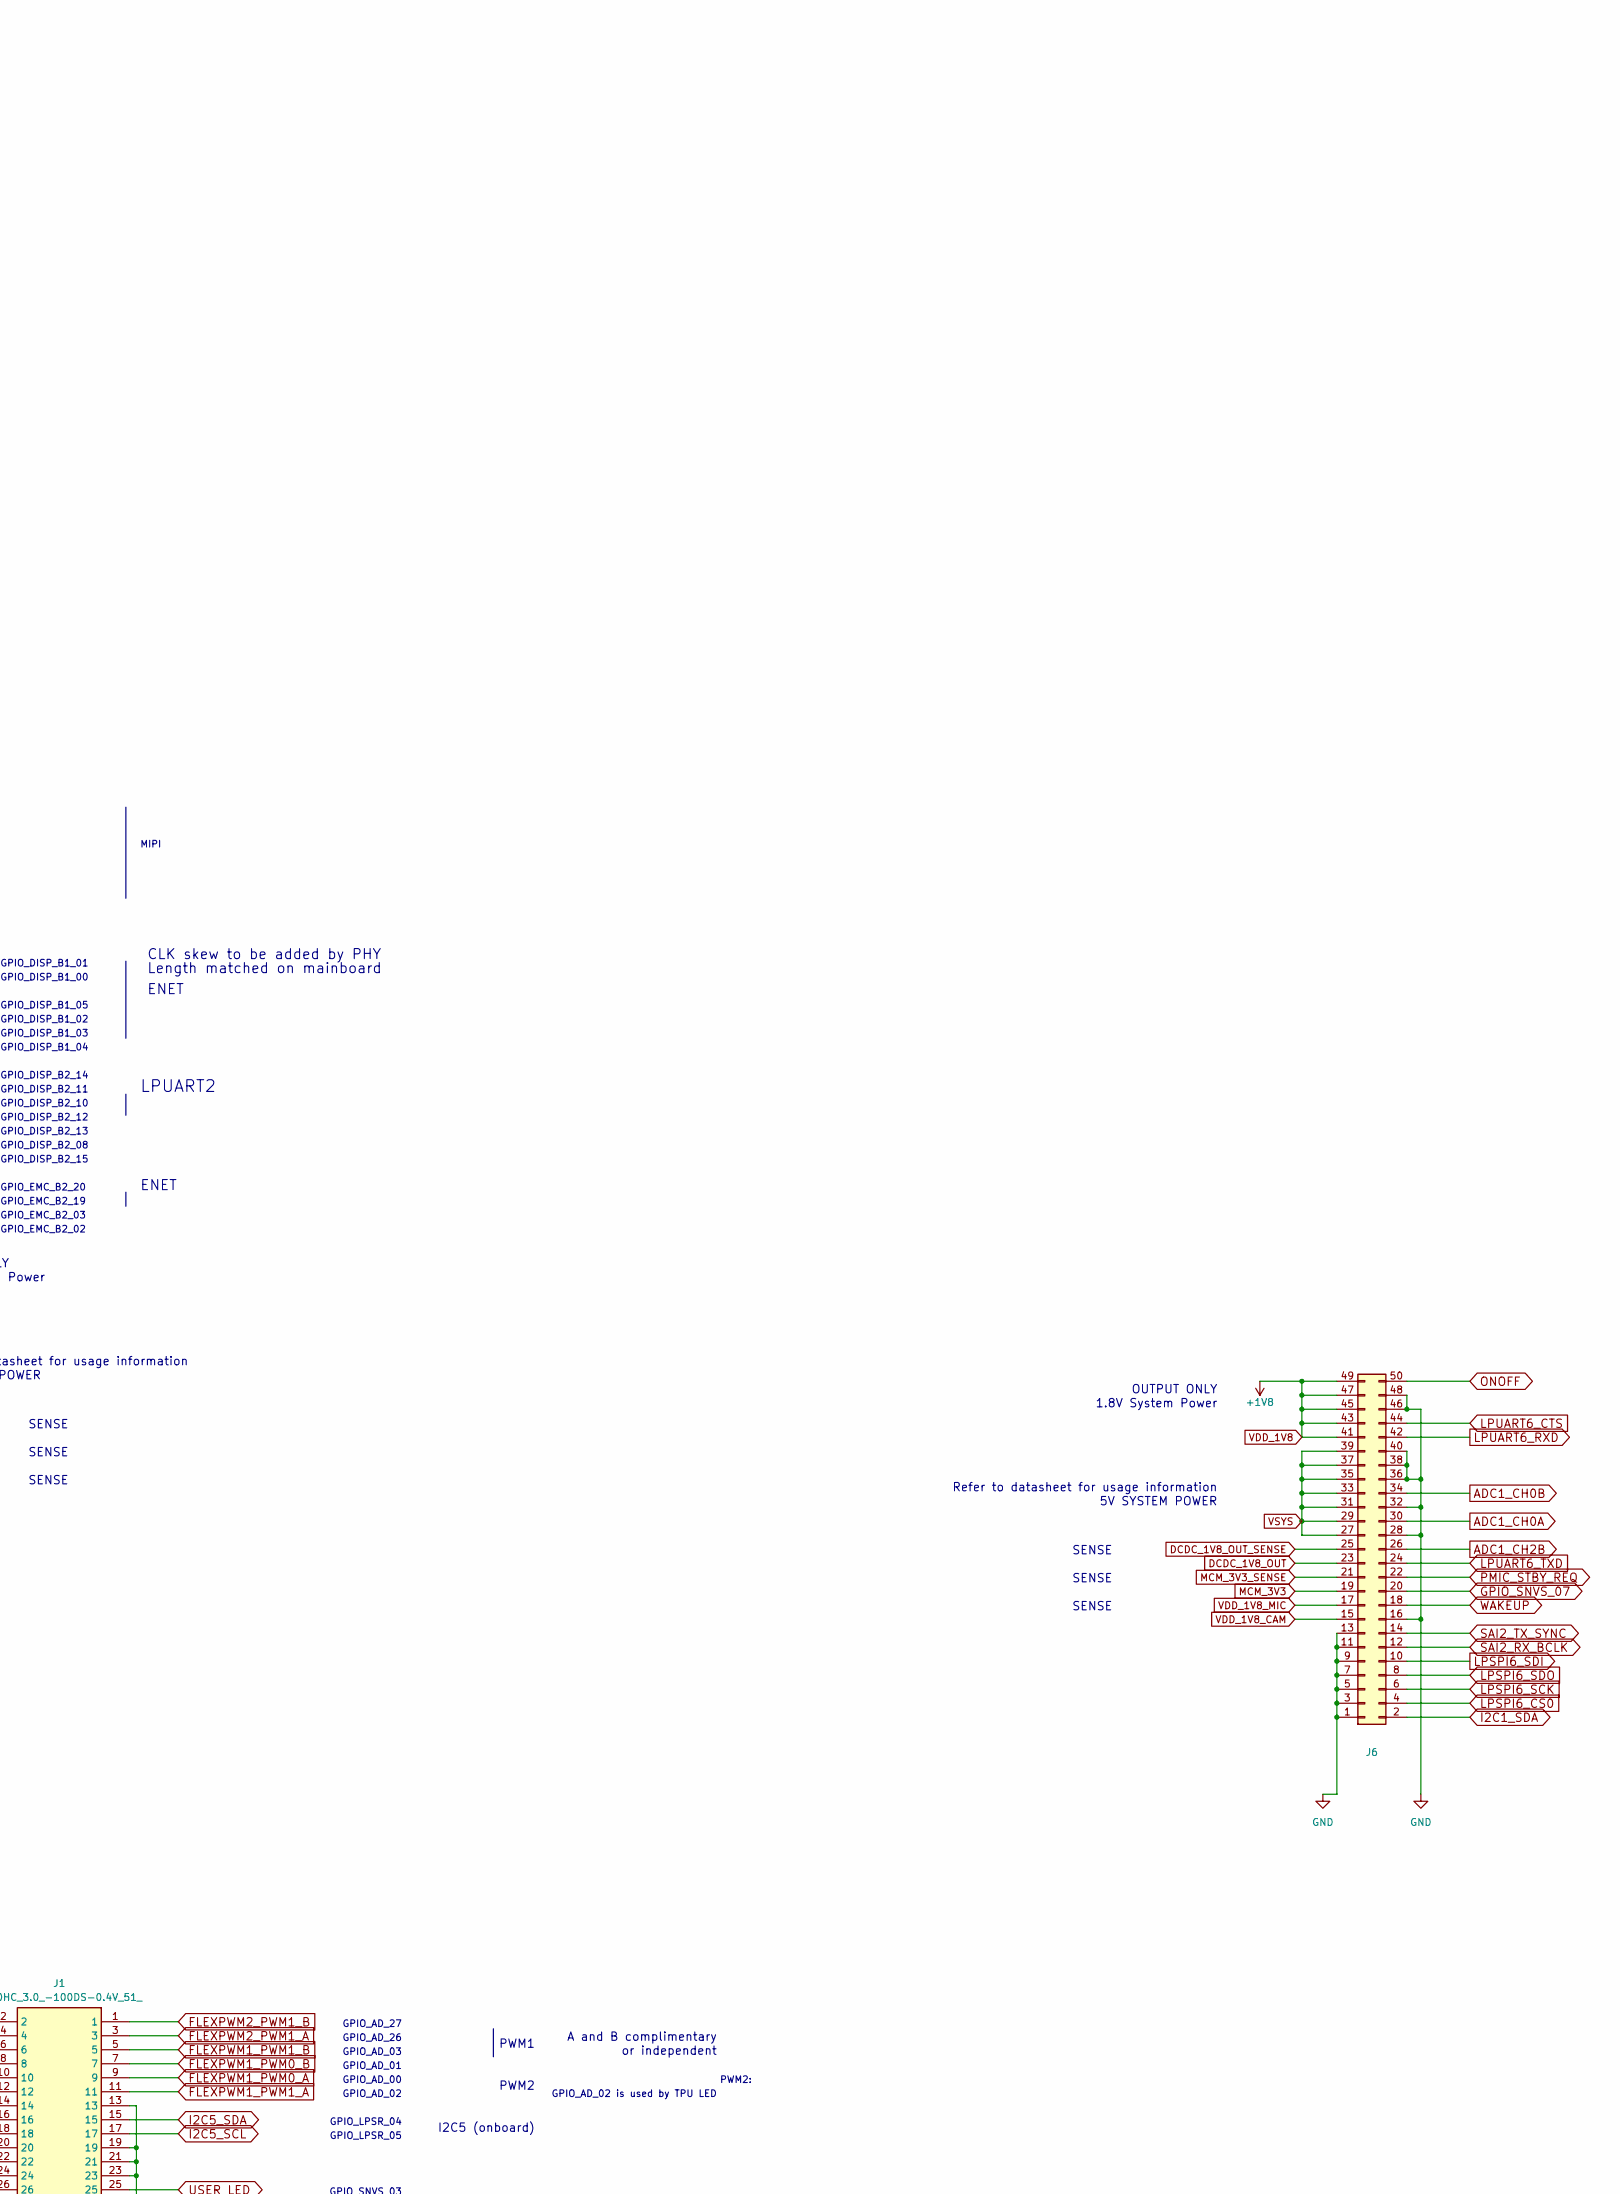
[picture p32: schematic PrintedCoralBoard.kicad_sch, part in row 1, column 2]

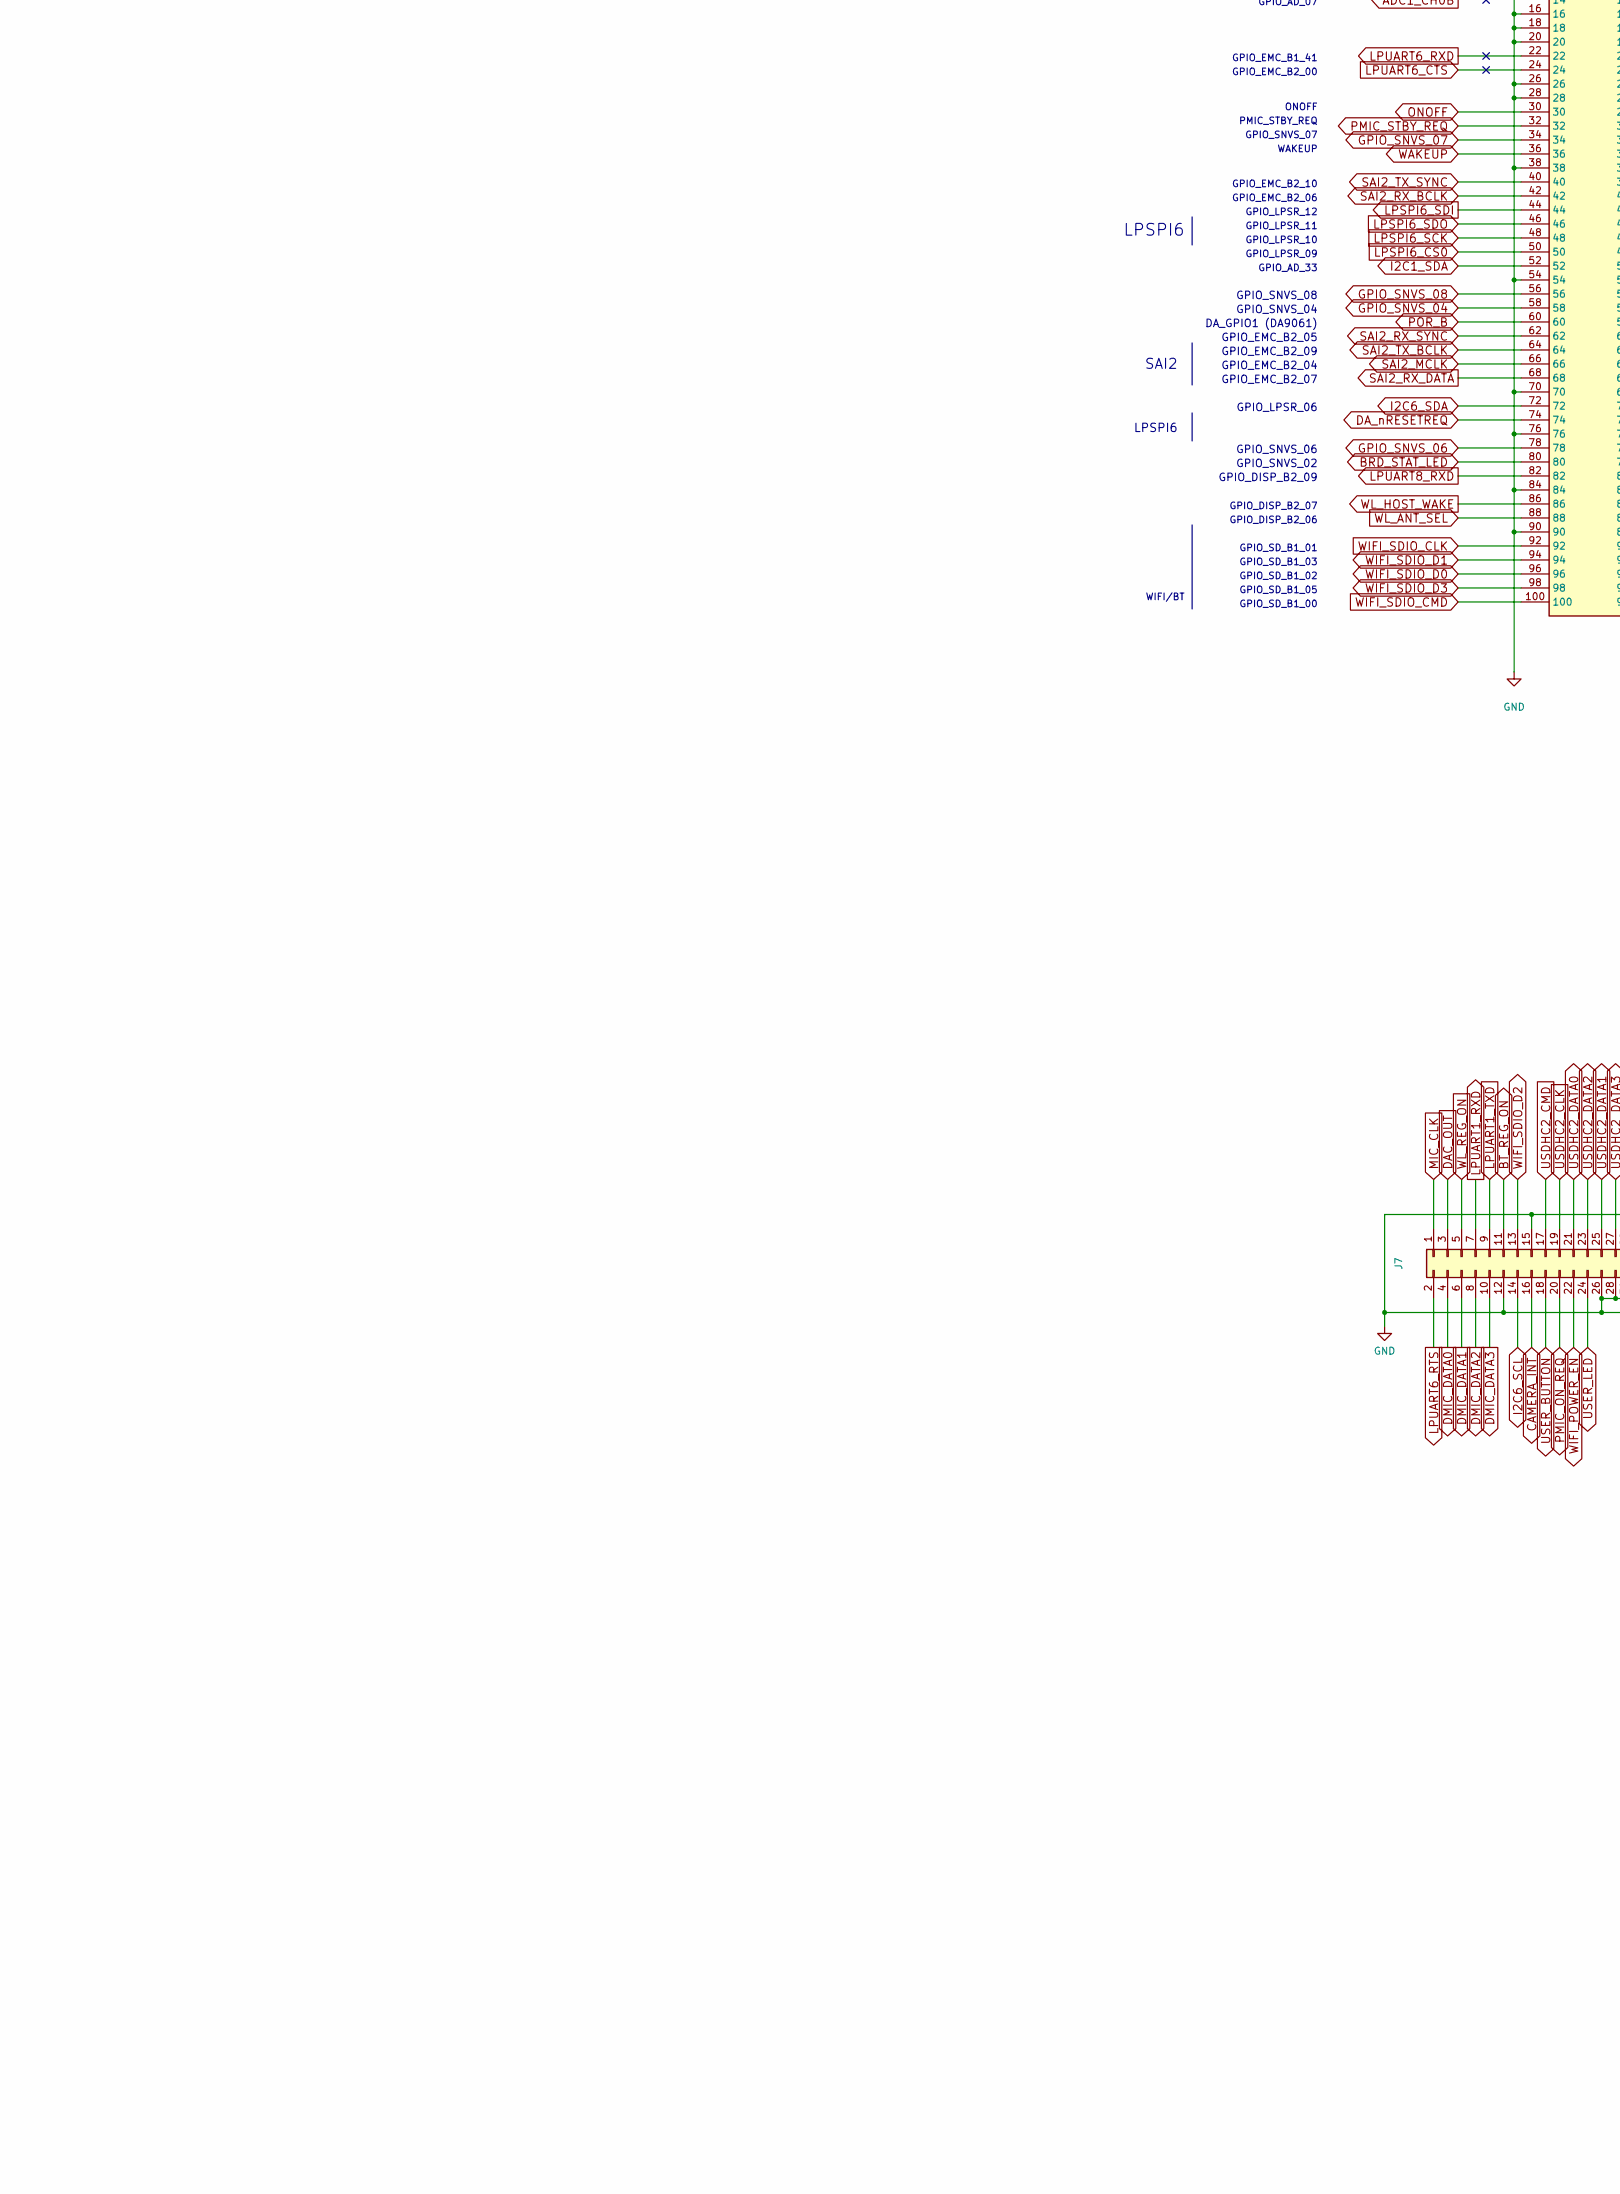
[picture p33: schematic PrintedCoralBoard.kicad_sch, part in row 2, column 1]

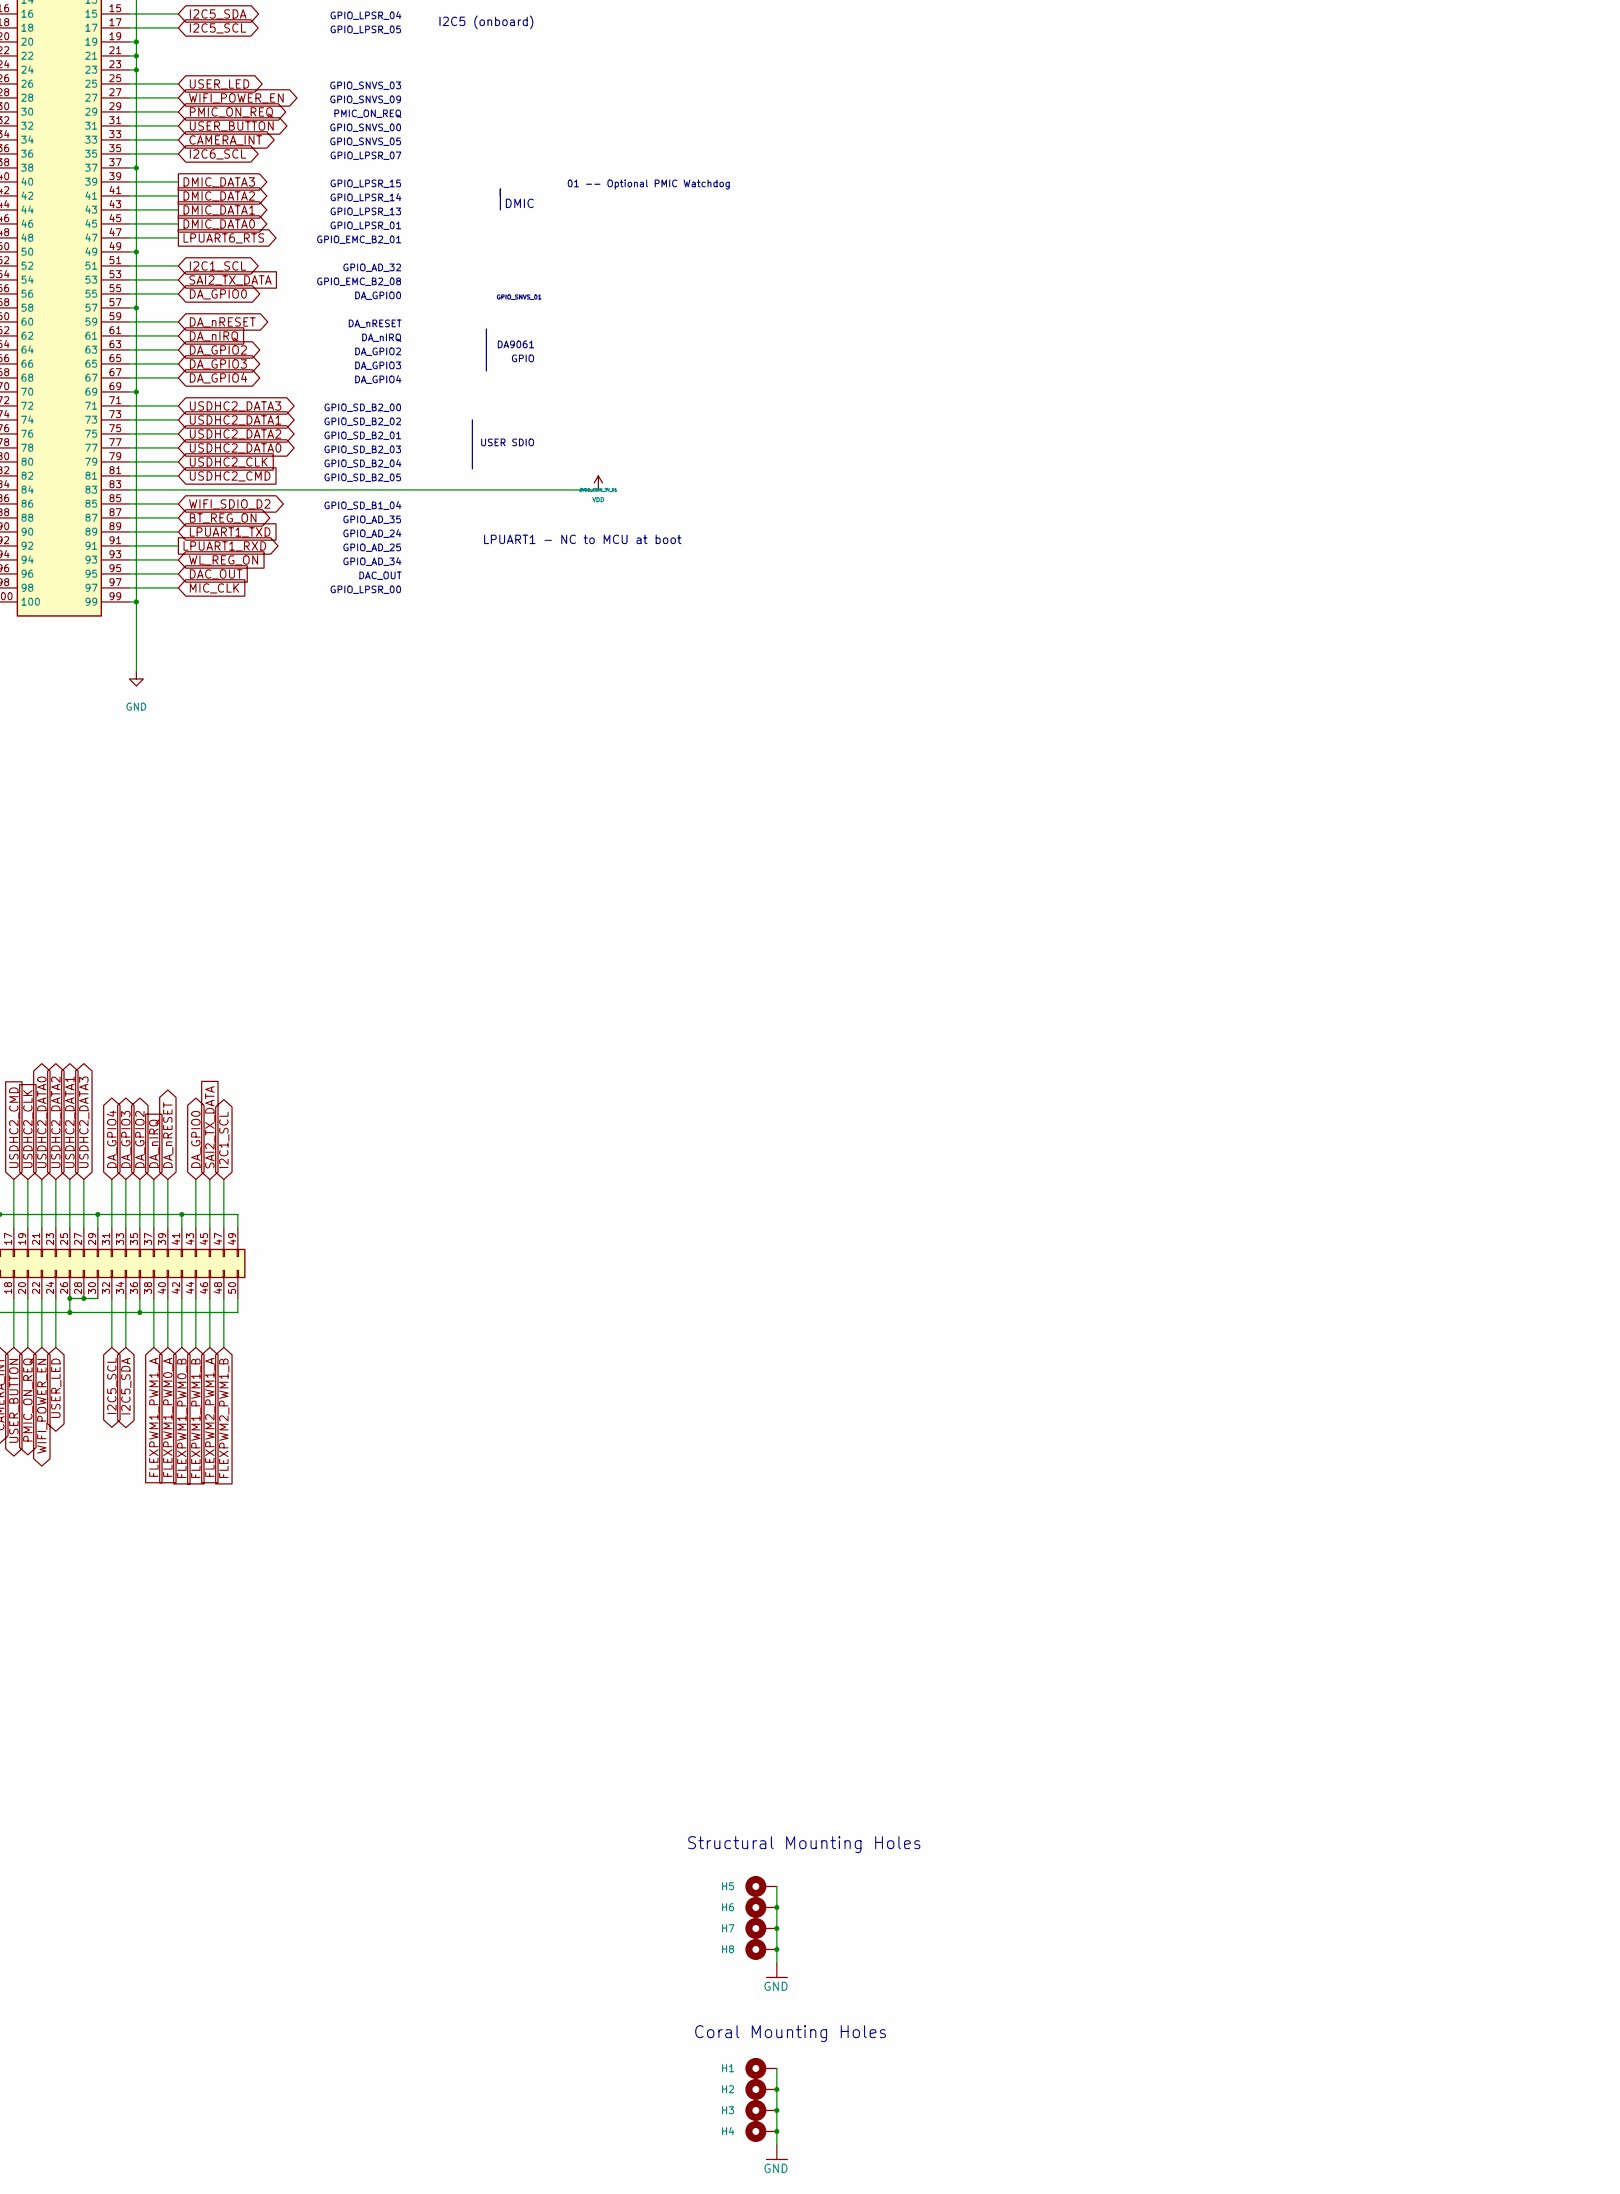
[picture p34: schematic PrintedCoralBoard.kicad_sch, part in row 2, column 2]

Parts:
H1, H2, H3, H4: MountingHole_Pad; CoralLandingPad
H5, H6, H7, H8: MountingHole_Pad; MountingHole_3.2mm_M3_DIN965_Pad
J1, J2: DF40HC_3.0_-100DS-0.4V_51_; DF40HC30100DS04V51; Manufacturer_Part_Number DF40HC(3.0)-100DS-0.4V(51)
J4, J5, J6, J7: Conn_02x25_Odd_Even; PinHeader_2x25_P2.54mm_Vertical; LCSC Part Number C350296

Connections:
ADC1_CH0A: J1.10, J6.30
ADC1_CH0B: J1.14, J6.34
ADC1_CH2B: J1.6, J6.26
BOOT_MODE0: J2.19, J4.39
BOOT_MODE1: J2.21, J4.37
BRD_STAT_LED: J1.80, J4.10
BT_DEV_WAKE: J2.62, J5.32
BT_HOST_WAKE: J2.50, J5.20
BT_REG_ON: J1.87, J7.11
CAMERA_INT: J1.33, J7.16
DAC_OUT: J1.95, J7.3
DA_GPIO0: J1.55, J7.43
DA_GPIO2: J1.63, J7.35
DA_GPIO3: J1.65, J7.33
DA_GPIO4: J1.67, J7.31
DA_nIRQ: J1.61, J7.37
DA_nRESET: J1.59, J7.39
DA_nRESETREQ: J1.74, J4.4
DCDC_1V8_OUT: J2.10, J6.23
DCDC_1V8_OUT_SENSE: J2.12, J6.25
DMIC_DATA0: J1.45, J7.4
DMIC_DATA1: J1.43, J7.6
DMIC_DATA2: J1.41, J7.8
DMIC_DATA3: J1.39, J7.10
ENET_RGMII_MDC: J2.44, J5.14
ENET_RGMII_MDIO: J2.46, J5.16
ENET_RGMII_RXC: J2.78, J5.13
ENET_RGMII_RXD0: J2.70, J5.5
ENET_RGMII_RXD1: J2.68, J5.3
ENET_RGMII_RXD2: J2.66, J5.1
ENET_RGMII_RXD3: J2.72, J5.7
ENET_RGMII_RX_EN: J2.76, J5.11
ENET_RGMII_TXC: J2.65, J4.1
ENET_RGMII_TXD0: J2.61, J4.5
ENET_RGMII_TXD1: J2.59, J4.7
ENET_RGMII_TXD2: J2.57, J4.9
ENET_RGMII_TXD3: J2.55, J4.11
ENET_RGMII_TX_EN: J2.63, J4.3
ETHPHY_RST_B: J2.42, J5.12
FLEXPWM1_PWM0_A: J1.9, J7.40
FLEXPWM1_PWM0_B: J1.7, J7.42
FLEXPWM1_PWM1_A: J1.11, J7.38
FLEXPWM1_PWM1_B: J1.5, J7.44
FLEXPWM2_PWM1_A: J1.3, J7.46
FLEXPWM2_PWM1_B: J1.1, J7.48
GND: H1.1, H2.1, H3.1, H4.1, H5.1, H6.1, H7.1, H8.1, J1.4, J1.8, J1.12, J1.13, J1.16, J1.18, J1.19, J1.20, J1.21, J1.23, J1.26, J1.28, J1.37, J1.38, J1.49, J1.54, J1.57, J1.69, J1.70, J1.76, J1.84, J1.90, J1.99, J2.7, J2.9, J2.11, J2.15, J2.17, J2.38, J2.43, J2.48, J2.49, J2.51, J2.53, J2.64, J2.67, J2.74, J2.77, J2.80, J2.82, J2.83, J2.84, J2.89, J2.90, J2.95, J2.96, J2.97, J2.99, J4.6, J4.14, J4.20, J4.23, J4.32, J4.34, J4.41, J4.50, J5.2, J5.4, J5.6, J5.8, J5.9, J5.15, J5.18, J5.21, J5.27, J5.33, J5.34, J5.36, J5.38, J5.39, J5.40, J5.42, J5.45, J6.1, J6.3, J6.5, J6.7, J6.9, J6.11, J6.13, J6.16, J6.28, J6.32, J6.36, J6.38, J6.40, J6.46, J6.48, J7.12, J7.15, J7.26, J7.28, J7.29, J7.30, J7.36, J7.41, J7.49, J7.50
GPIO_SNVS_04: J1.58, J4.46
GPIO_SNVS_06: J1.78, J4.8
GPIO_SNVS_07: J1.34, J6.20
GPIO_SNVS_08: J1.56, J4.48
I2C1_SCL: J1.51, J7.47
I2C1_SDA: J1.52, J6.2
I2C5_SCL: J1.17, J7.32
I2C5_SDA: J1.15, J7.34
I2C6_SCL: J1.35, J7.14
I2C6_SDA: J1.72, J4.2
LPSPI1_PCS0: J2.71, J5.48
LPSPI1_SCK: J2.69, J5.50
LPSPI1_SDI: J2.75, J5.44
LPSPI1_SDO: J2.73, J5.46
LPSPI6_CS0: J1.50, J6.4
LPSPI6_SCK: J1.48, J6.6
LPSPI6_SDI: J1.44, J6.10
LPSPI6_SDO: J1.46, J6.8
LPUART1_RXD: J1.91, J7.7
LPUART1_TXD: J1.89, J7.9
LPUART2_CTS_B: J2.56, J5.26
LPUART2_RTS_B: J2.54, J5.24
LPUART2_RXD: J2.60, J5.30
LPUART2_TXD: J2.58, J5.28
LPUART6_CTS: J1.24, J6.44
LPUART6_RTS: J1.47, J7.2
LPUART6_RXD: J1.22, J6.42
LPUART6_TXD: J1.2, J6.24
LPUART8_RXD: J1.82, J4.12
LPUART8_TXD: J2.52, J5.22
MCM_3V3: J2.6, J6.19
MCM_3V3_SENSE: J2.8, J6.21
MIC_CLK: J1.97, J7.1
MIPI_CSI_CK_N: J2.94, J5.25
MIPI_CSI_CK_P: J2.92, J5.23
MIPI_CSI_D0_N: J2.88, J5.19
MIPI_CSI_D0_P: J2.86, J5.17
MIPI_CSI_D1_N: J2.100, J5.31
MIPI_CSI_D1_P: J2.98, J5.29
MIPI_DSI_CK_N: J2.87, J5.41
MIPI_DSI_CK_P: J2.85, J5.43
MIPI_DSI_D0_N: J2.81, J5.47
MIPI_DSI_D0_P: J2.79, J5.49
MIPI_DSI_D1_N: J2.93, J5.35
MIPI_DSI_D1_P: J2.91, J5.37
ONOFF: J1.30, J6.50
PMIC_ON_REQ: J1.29, J7.20
PMIC_STBY_REQ: J1.32, J6.22
POR_B: J1.60, J4.44
RGMII1_PHY_INTB: J2.40, J5.10
SAI2_MCLK: J1.66, J4.38
SAI2_RX_BCLK: J1.42, J6.12
SAI2_RX_DATA: J1.68, J4.36
SAI2_RX_SYNC: J1.62, J4.42
SAI2_TX_BCLK: J1.64, J4.40
SAI2_TX_DATA: J1.53, J7.45
SAI2_TX_SYNC: J1.40, J6.14
USDHC2_CLK: J1.79, J7.19
USDHC2_CMD: J1.81, J7.17
USDHC2_DATA0: J1.77, J7.21
USDHC2_DATA1: J1.73, J7.25
USDHC2_DATA2: J1.75, J7.23
USDHC2_DATA3: J1.71, J7.27
USER_BUTTON: J1.31, J7.18
USER_LED: J1.25, J7.24
VDD: J1.83
VDDA_1P0_01: J2.5, J4.45
VDD_1V8: J2.28, J2.30, J2.32, J2.34, J2.36, J2.47, J4.13, J4.15, J4.17, J4.19, J6.41, J6.43, J6.45, J6.47, J6.49
VDD_1V8_AON: J2.3, J4.47
VDD_1V8_CAM: J2.2, J6.15
VDD_1V8_MIC: J2.4, J6.17
VDD_1V8_SENSE: J2.45, J4.21
VDD_2V8_CAM: J2.1, J4.49
VDD_3V3: J2.33, J2.35, J2.37, J2.39, J2.41, J4.25, J4.27, J4.29, J4.31, J4.33
VDD_3V3_SENSE: J2.31, J4.35
VDD_LPSR_IN_01: J2.13, J4.43
VSYS: J2.14, J2.16, J2.18, J2.20, J2.22, J2.24, J2.26, J6.27, J6.29, J6.31, J6.33, J6.35, J6.37, J6.39
WAKEUP: J1.36, J6.18
WIFI_POWER_EN: J1.27, J7.22
WIFI_SDIO_CLK: J1.92, J4.22
WIFI_SDIO_CMD: J1.100, J4.30
WIFI_SDIO_D0: J1.96, J4.26
WIFI_SDIO_D1: J1.94, J4.24
WIFI_SDIO_D2: J1.85, J7.13
WIFI_SDIO_D3: J1.98, J4.28
WL_ANT_SEL: J1.88, J4.18
WL_HOST_WAKE: J1.86, J4.16
WL_REG_ON: J1.93, J7.5

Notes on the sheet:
SYSTEM 1.8V
GPIO_AD_03
SENSE
GPIO_DISP_B1_05
GPIO_SD_B2_05
GPIO_AD_29
Odd pins 23-29 > SPARE PINS
ONOFF
GPIO_AD_01
GPIO_AD_32
GPIO_AD_33
USER SDIO
GPIO_AD_27
GPIO_DISP_B1_03
GPIO_DISP_B2_08
GPIO_SNVS_08
GPIO_EMC_B2_19
GPIO_AD_26
GPIO_SNVS_09
GPIO_AD_28
GPIO_EMC_B1_41
GPIO_LPSR_05
GPIO_SD_B2_00
GPIO_SD_B1_03
GPIO_DISP_B2_11
GPIO_DISP_B2_13
GPIO_LPSR_00
GPIO_DISP_B2_10
GPIO_EMC_B2_10
GPIO_DISP_B2_07
Refer to datasheet for usage information
Coral Mounting Holes
NOT FOR GENERAL USE
DA_GPIO3
SAI2
GPIO_DISP_B1_07
GPIO_DISP_B2_06
GPIO_SD_B1_02
GPIO_LPSR_13
GPIO_EMC_B2_00

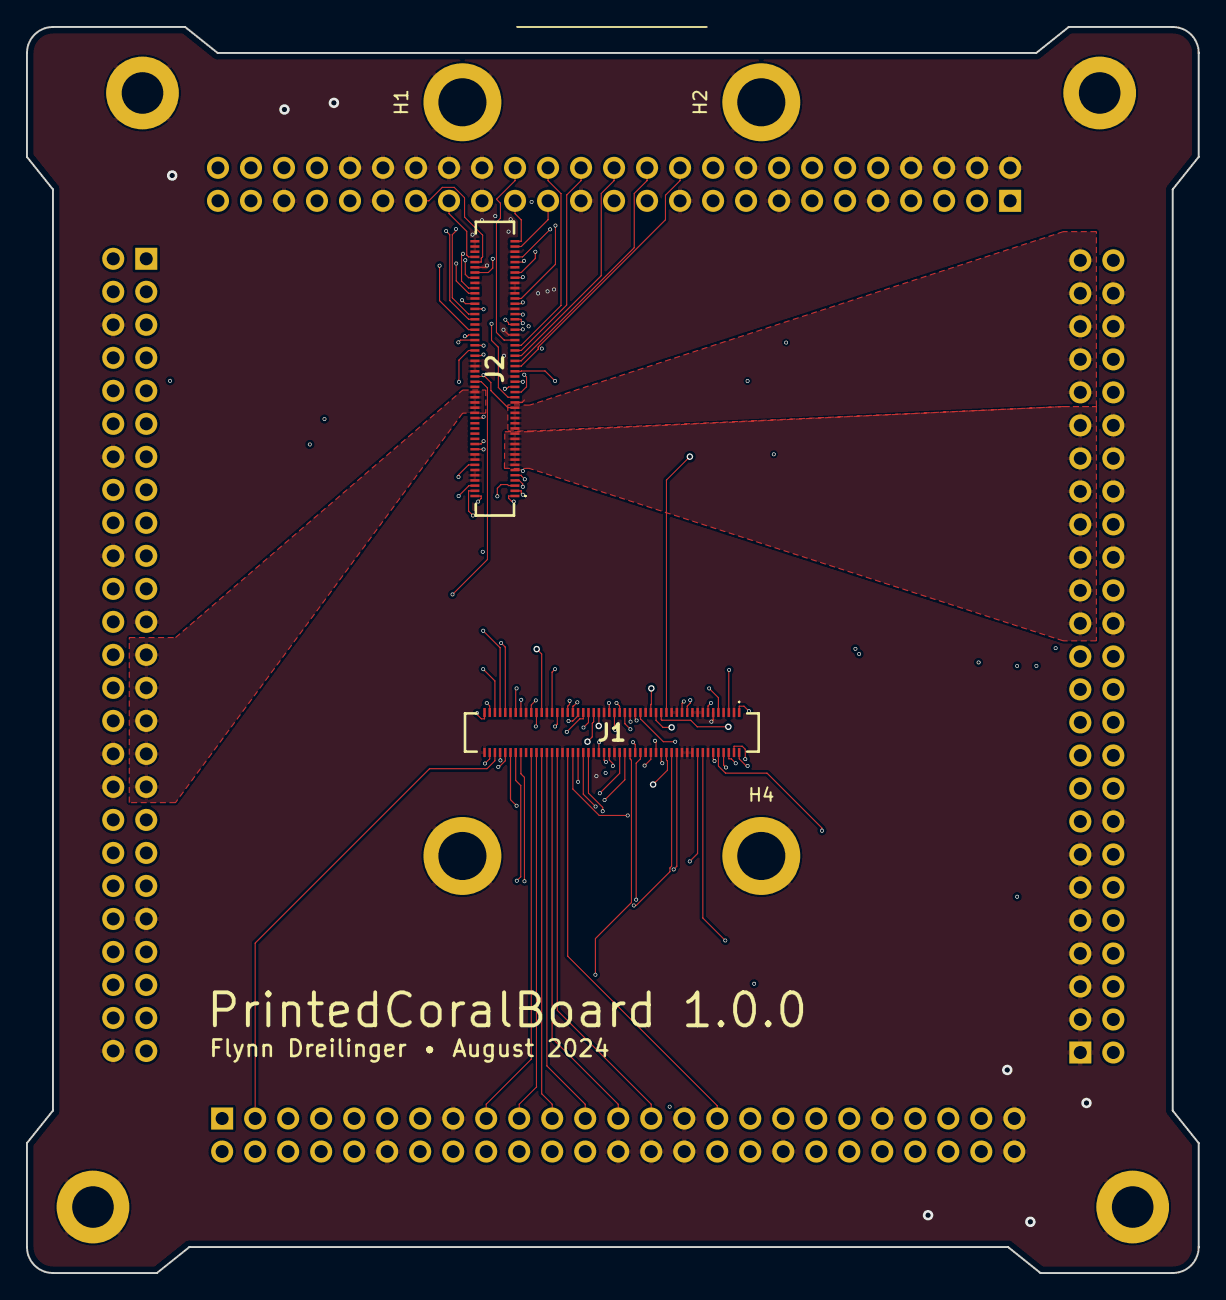
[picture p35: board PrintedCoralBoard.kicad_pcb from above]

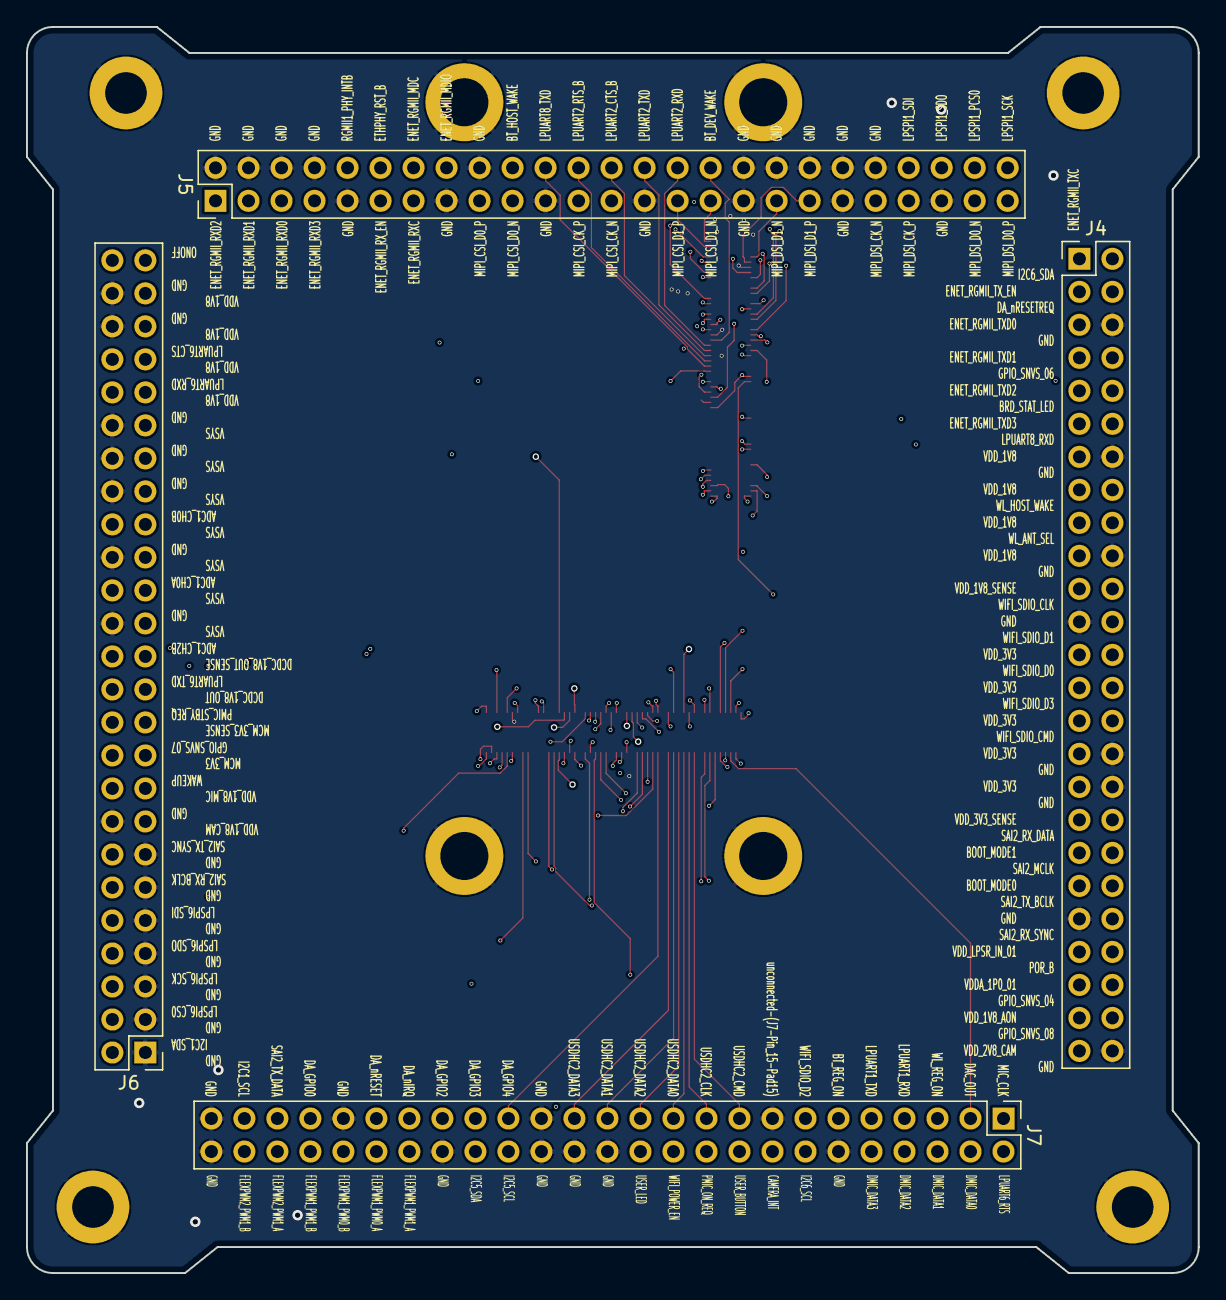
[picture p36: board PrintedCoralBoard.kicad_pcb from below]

Board: 4 copper layers, 90.2 x 95.9 mm, 14 parts (4 on the bottom side), 133 nets.

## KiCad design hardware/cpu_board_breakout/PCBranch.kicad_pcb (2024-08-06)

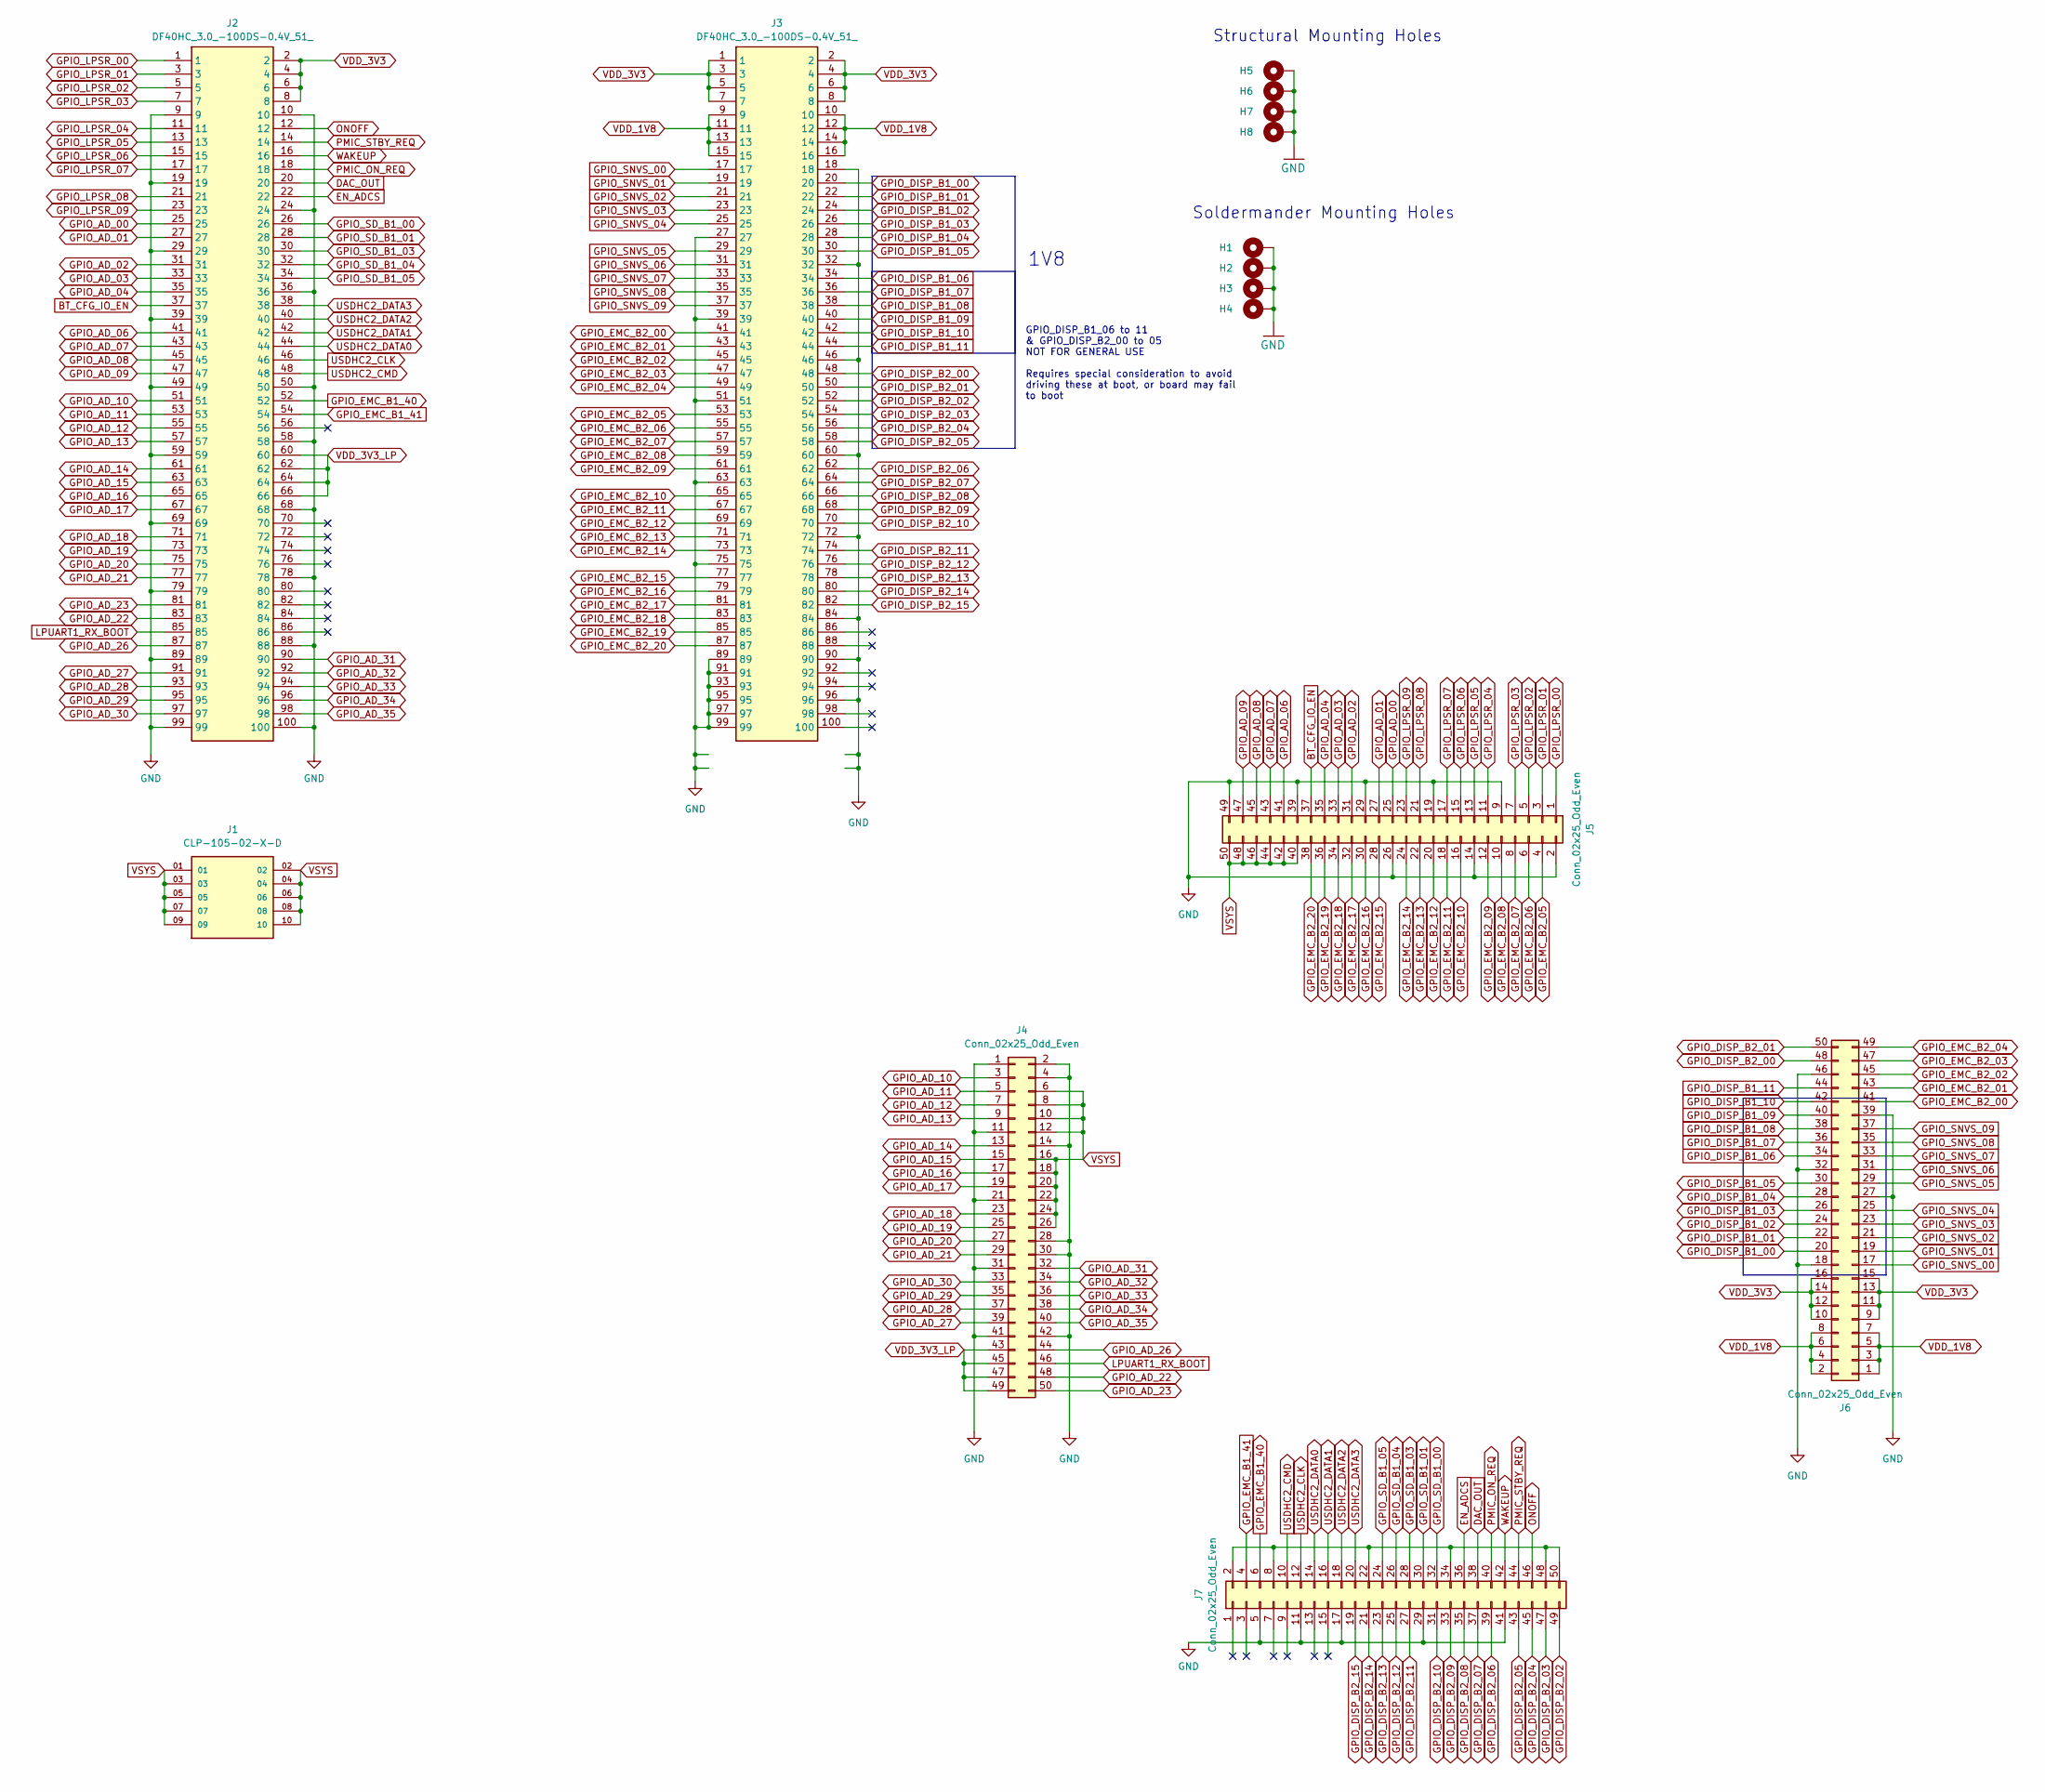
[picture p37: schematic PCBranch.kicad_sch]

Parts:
H1, H2, H3, H4: MountingHole_Pad; MountingHole_2.7mm_M2.5_DIN965_Pad
H5, H6, H7, H8: MountingHole_Pad; MountingHole_3.2mm_M3_DIN965_Pad
J1: CLP-105-02-X-D; SAMTEC_CLP-105-02-X-D; PARTREV V
J2, J3: DF40HC_3.0_-100DS-0.4V_51_; DF40HC30100DS04V51; Manufacturer_Part_Number DF40HC(3.0)-100DS-0.4V(51)
J4, J5, J6, J7: Conn_02x25_Odd_Even; PinHeader_2x25_P2.54mm_Vertical; LCSC Part Number C350296

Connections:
BT_CFG_IO_EN: J2.37, J5.37
DAC_OUT: J2.20, J7.38
EN_ADCS: J2.22, J7.36
GND: H1.1, H2.1, H3.1, H4.1, H5.1, H6.1, H7.1, H8.1, J2.9, J2.10, J2.19, J2.24, J2.29, J2.36, J2.39, J2.49, J2.50, J2.58, J2.59, J2.68, J2.69, J2.78, J2.79, J2.88, J2.89, J2.99, J2.100, J3.18, J3.27, J3.32, J3.39, J3.46, J3.51, J3.60, J3.63, J3.72, J3.75, J3.84, J3.89, J3.90, J3.91, J3.93, J3.95, J3.96, J3.97, J3.99, J4.1, J4.2, J4.4, J4.11, J4.14, J4.21, J4.28, J4.30, J4.31, J4.41, J4.42, J5.2, J5.9, J5.14, J5.19, J5.26, J5.29, J5.39, J5.49, J6.18, J6.27, J6.32, J6.39, J6.46, J7.5, J7.11, J7.17, J7.29, J7.41
GPIO_AD_00: J2.25, J5.25
GPIO_AD_01: J2.27, J5.27
GPIO_AD_02: J2.31, J5.31
GPIO_AD_03: J2.33, J5.33
GPIO_AD_04: J2.35, J5.35
GPIO_AD_06: J2.41, J5.41
GPIO_AD_07: J2.43, J5.43
GPIO_AD_08: J2.45, J5.45
GPIO_AD_09: J2.47, J5.47
GPIO_AD_10: J2.51, J4.3
GPIO_AD_11: J2.53, J4.5
GPIO_AD_12: J2.55, J4.7
GPIO_AD_13: J2.57, J4.9
GPIO_AD_14: J2.61, J4.13
GPIO_AD_15: J2.63, J4.15
GPIO_AD_16: J2.65, J4.17
GPIO_AD_17: J2.67, J4.19
GPIO_AD_18: J2.71, J4.23
GPIO_AD_19: J2.73, J4.25
GPIO_AD_20: J2.75, J4.27
GPIO_AD_21: J2.77, J4.29
GPIO_AD_22: J2.83, J4.48
GPIO_AD_23: J2.81, J4.50
GPIO_AD_26: J2.87, J4.44
GPIO_AD_27: J2.91, J4.39
GPIO_AD_28: J2.93, J4.37
GPIO_AD_29: J2.95, J4.35
GPIO_AD_30: J2.97, J4.33
GPIO_AD_31: J2.90, J4.32
GPIO_AD_32: J2.92, J4.34
GPIO_AD_33: J2.94, J4.36
GPIO_AD_34: J2.96, J4.38
GPIO_AD_35: J2.98, J4.40
GPIO_DISP_B1_00: J3.20, J6.20
GPIO_DISP_B1_01: J3.22, J6.22
GPIO_DISP_B1_02: J3.24, J6.24
GPIO_DISP_B1_03: J3.26, J6.26
GPIO_DISP_B1_04: J3.28, J6.28
GPIO_DISP_B1_05: J3.30, J6.30
GPIO_DISP_B1_06: J3.34, J6.34
GPIO_DISP_B1_07: J3.36, J6.36
GPIO_DISP_B1_08: J3.38, J6.38
GPIO_DISP_B1_09: J3.40, J6.40
GPIO_DISP_B1_10: J3.42, J6.42
GPIO_DISP_B1_11: J3.44, J6.44
GPIO_DISP_B2_00: J3.48, J6.48
GPIO_DISP_B2_01: J3.50, J6.50
GPIO_DISP_B2_02: J3.52, J7.49
GPIO_DISP_B2_03: J3.54, J7.47
GPIO_DISP_B2_04: J3.56, J7.45
GPIO_DISP_B2_05: J3.58, J7.43
GPIO_DISP_B2_06: J3.62, J7.39
GPIO_DISP_B2_07: J3.64, J7.37
GPIO_DISP_B2_08: J3.66, J7.35
GPIO_DISP_B2_09: J3.68, J7.33
GPIO_DISP_B2_10: J3.70, J7.31
GPIO_DISP_B2_11: J3.74, J7.27
GPIO_DISP_B2_12: J3.76, J7.25
GPIO_DISP_B2_13: J3.78, J7.23
GPIO_DISP_B2_14: J3.80, J7.21
GPIO_DISP_B2_15: J3.82, J7.19
GPIO_EMC_B1_40: J2.52, J7.6
GPIO_EMC_B1_41: J2.54, J7.4
GPIO_EMC_B2_00: J3.41, J6.41
GPIO_EMC_B2_01: J3.43, J6.43
GPIO_EMC_B2_02: J3.45, J6.45
GPIO_EMC_B2_03: J3.47, J6.47
GPIO_EMC_B2_04: J3.49, J6.49
GPIO_EMC_B2_05: J3.53, J5.4
GPIO_EMC_B2_06: J3.55, J5.6
GPIO_EMC_B2_07: J3.57, J5.8
GPIO_EMC_B2_08: J3.59, J5.10
GPIO_EMC_B2_09: J3.61, J5.12
GPIO_EMC_B2_10: J3.65, J5.16
GPIO_EMC_B2_11: J3.67, J5.18
GPIO_EMC_B2_12: J3.69, J5.20
GPIO_EMC_B2_13: J3.71, J5.22
GPIO_EMC_B2_14: J3.73, J5.24
GPIO_EMC_B2_15: J3.77, J5.28
GPIO_EMC_B2_16: J3.79, J5.30
GPIO_EMC_B2_17: J3.81, J5.32
GPIO_EMC_B2_18: J3.83, J5.34
GPIO_EMC_B2_19: J3.85, J5.36
GPIO_EMC_B2_20: J3.87, J5.38
GPIO_LPSR_00: J2.1, J5.1
GPIO_LPSR_01: J2.3, J5.3
GPIO_LPSR_02: J2.5, J5.5
GPIO_LPSR_03: J2.7, J5.7
GPIO_LPSR_04: J2.11, J5.11
GPIO_LPSR_05: J2.13, J5.13
GPIO_LPSR_06: J2.15, J5.15
GPIO_LPSR_07: J2.17, J5.17
GPIO_LPSR_08: J2.21, J5.21
GPIO_LPSR_09: J2.23, J5.23
GPIO_SD_B1_00: J2.26, J7.32
GPIO_SD_B1_01: J2.28, J7.30
GPIO_SD_B1_03: J2.30, J7.28
GPIO_SD_B1_04: J2.32, J7.26
GPIO_SD_B1_05: J2.34, J7.24
GPIO_SNVS_00: J3.17, J6.17
GPIO_SNVS_01: J3.19, J6.19
GPIO_SNVS_02: J3.21, J6.21
GPIO_SNVS_03: J3.23, J6.23
GPIO_SNVS_04: J3.25, J6.25
GPIO_SNVS_05: J3.29, J6.29
GPIO_SNVS_06: J3.31, J6.31
GPIO_SNVS_07: J3.33, J6.33
GPIO_SNVS_08: J3.35, J6.35
GPIO_SNVS_09: J3.37, J6.37
LPUART1_RX_BOOT: J2.85, J4.46
unnamed: J7.2, J7.8, J7.22, J7.34, J7.48, J7.50
ONOFF: J2.12, J7.46
PMIC_ON_REQ: J2.18, J7.40
PMIC_STBY_REQ: J2.14, J7.44
USDHC2_CLK: J2.46, J7.12
USDHC2_CMD: J2.48, J7.10
USDHC2_DATA0: J2.44, J7.14
USDHC2_DATA1: J2.42, J7.16
USDHC2_DATA2: J2.40, J7.18
USDHC2_DATA3: J2.38, J7.20
VDD_1V8: J3.9, J3.10, J3.11, J3.12, J3.13, J3.14, J3.15, J3.16, J6.1, J6.2, J6.3, J6.4, J6.5, J6.6, J6.7, J6.8
VDD_3V3: J2.2, J2.4, J2.6, J2.8, J3.1, J3.2, J3.3, J3.4, J3.5, J3.6, J3.7, J3.8, J6.9, J6.10, J6.11, J6.12, J6.13, J6.14, J6.15, J6.16
VDD_3V3_LP: J2.60, J2.62, J2.64, J2.66, J4.43, J4.45, J4.47, J4.49
VSYS: J1.01, J1.02, J1.03, J1.04, J1.05, J1.06, J1.07, J1.08, J1.09, J1.10, J4.6, J4.8, J4.10, J4.12, J4.16, J4.18, J4.20, J4.22, J4.24, J4.26, J5.40, J5.42, J5.44, J5.46, J5.48, J5.50
WAKEUP: J2.16, J7.42

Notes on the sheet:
1V8
Soldermander Mounting Holes
Structural Mounting Holes
GPIO_DISP_B1_06 to 11 & GPIO_DISP_B2_00 to 05 NOT FOR GENERAL USE Requires special consideration to avoid driving these at boot, or board may fail to boot

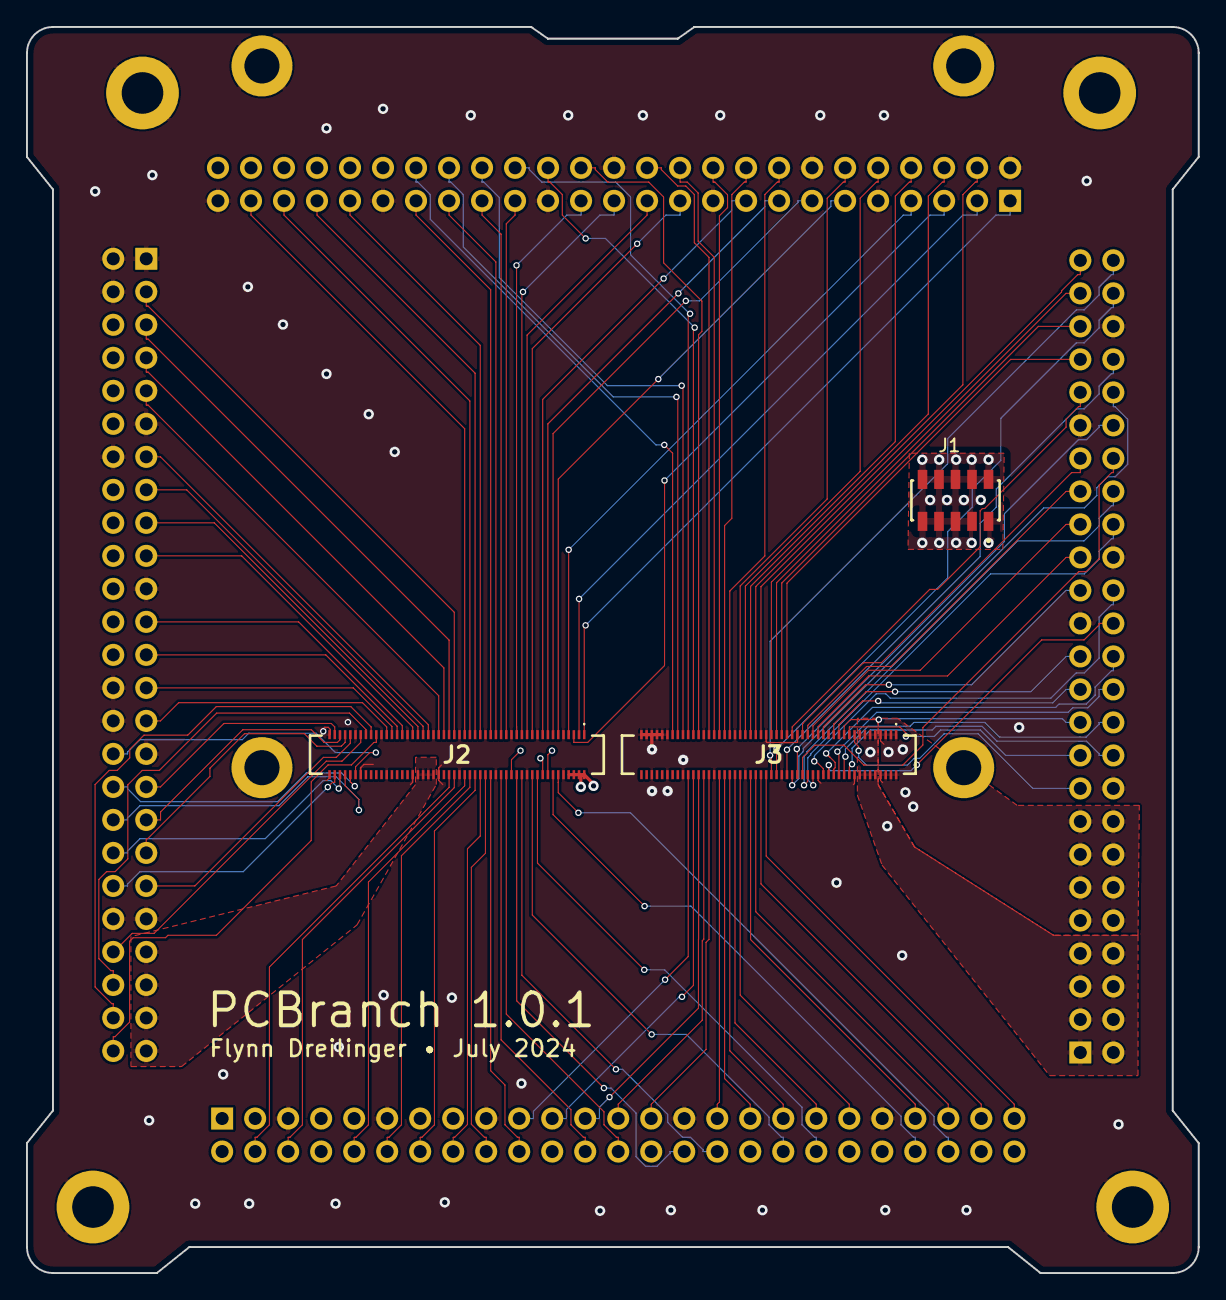
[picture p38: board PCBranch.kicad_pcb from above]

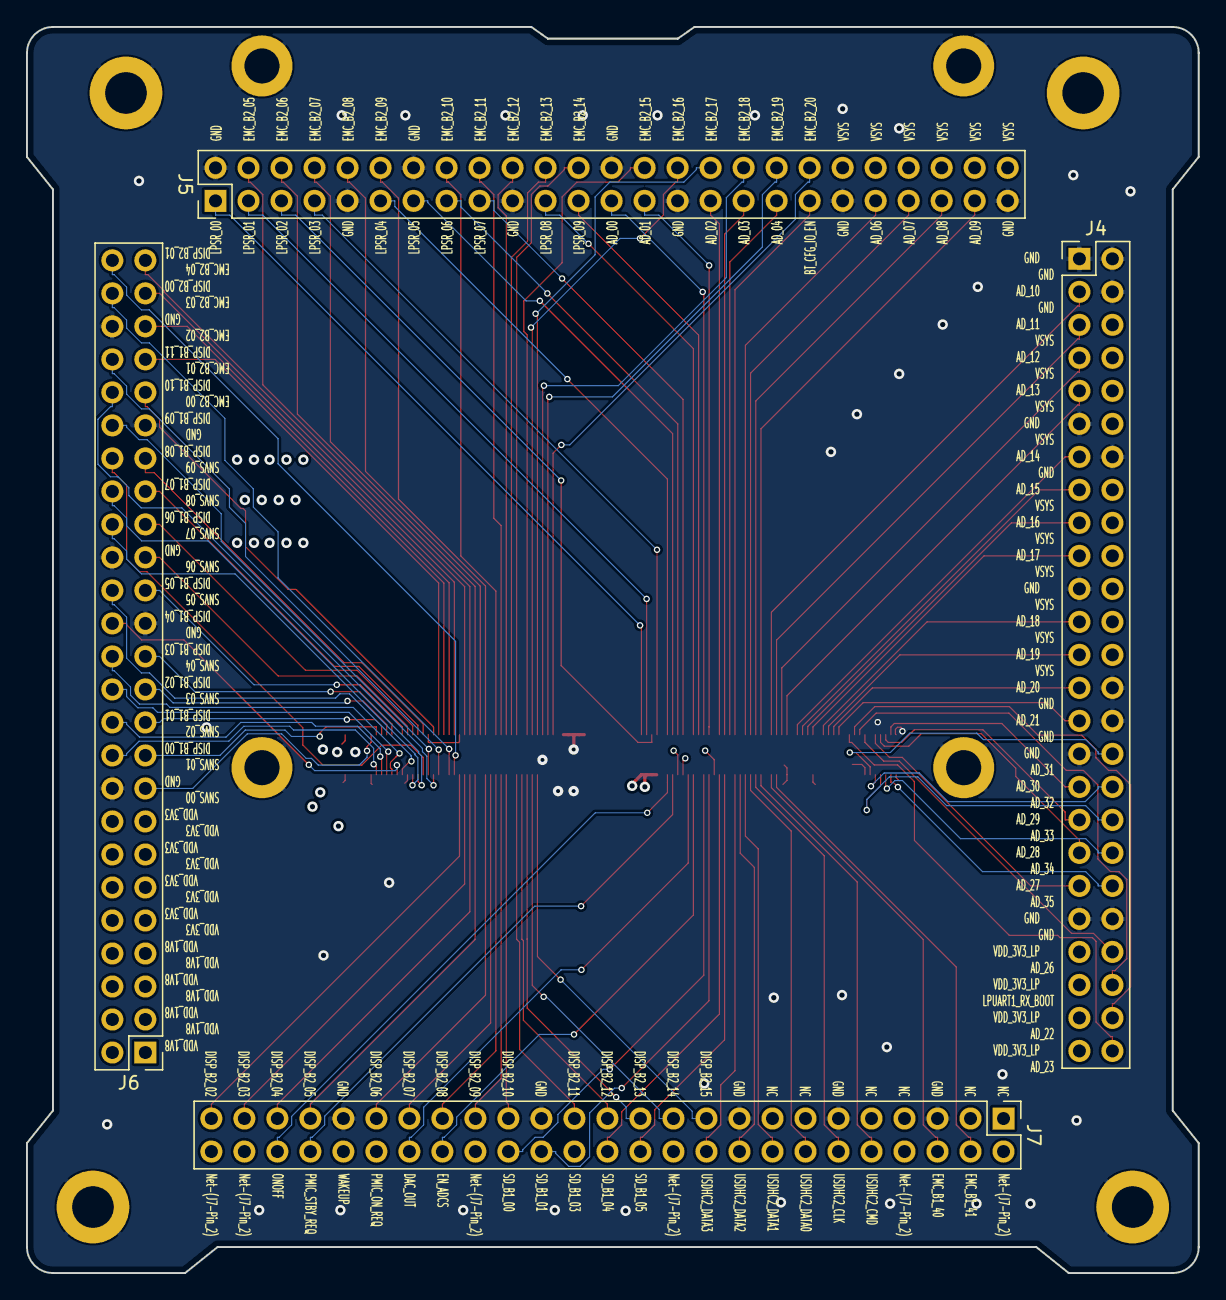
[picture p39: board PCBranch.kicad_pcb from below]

Board: 4 copper layers, 90.2 x 95.9 mm, 15 parts (4 on the bottom side), 129 nets.

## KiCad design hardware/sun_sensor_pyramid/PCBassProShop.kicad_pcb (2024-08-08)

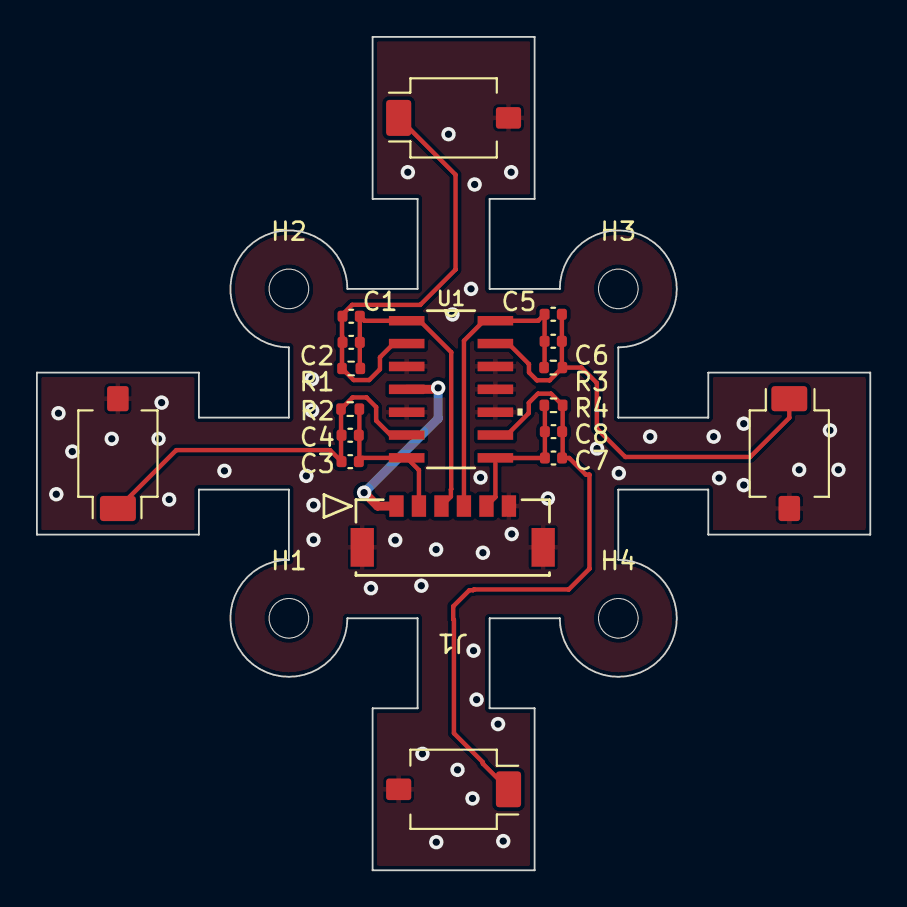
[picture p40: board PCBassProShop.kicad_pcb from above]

Board: 2 copper layers, 46.3 x 46.3 mm, 22 parts (0 on the bottom side), 10 nets.

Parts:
C1, C3, C5, C7: 1nF; C_0402_1005Metric
C2, C4, C6, C8: 100nF; C_0402_1005Metric
D1, D2, D3, D4: SFH2430; Osram_SFH2430
H1, H2, H3, H4: MountingHole_Pad; MountingHole_2.2mm_M2
J1: 5055670631; CON_5055670631
R1, R2, R3, R4: 3.9k; R_0402_1005Metric
U1: LTC2052IS_PBF; SO-14_S

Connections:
+3V3: J1.1, U1.4 (V+)
/OUT1: C1.2, C2.2, J1.3, R1.2, U1.1 (OUTA)
/OUT2: C3.2, C4.2, J1.2, R2.2, U1.7 (OUTB)
/OUT3: C7.2, C8.2, J1.5, R4.2, U1.8 (OUTC)
/OUT4: C5.2, C6.2, J1.4, R3.2, U1.14 (OUTD)
/Photodiode 1/IN-: C1.1, C2.1, D1.1 (K), R1.1, U1.2 (-INA)
/Photodiode 2/IN-: C3.1, C4.1, D2.1 (K), R2.1, U1.6 (-INB)
/Photodiode 3/IN-: C7.1, C8.1, D4.1 (K), R4.1, U1.9 (-INC)
/Photodiode 4/IN-: C5.1, C6.1, D3.1 (K), R3.1, U1.13 (-IND)
GND: D1.2 (A), D2.2 (A), D3.2 (A), D4.2 (A), J1.6, J1.7 (Shield), J1.8 (Shield), U1.3 (+INA), U1.5 (+INB), U1.10 (+INC), U1.11 (V-), U1.12 (+IND)

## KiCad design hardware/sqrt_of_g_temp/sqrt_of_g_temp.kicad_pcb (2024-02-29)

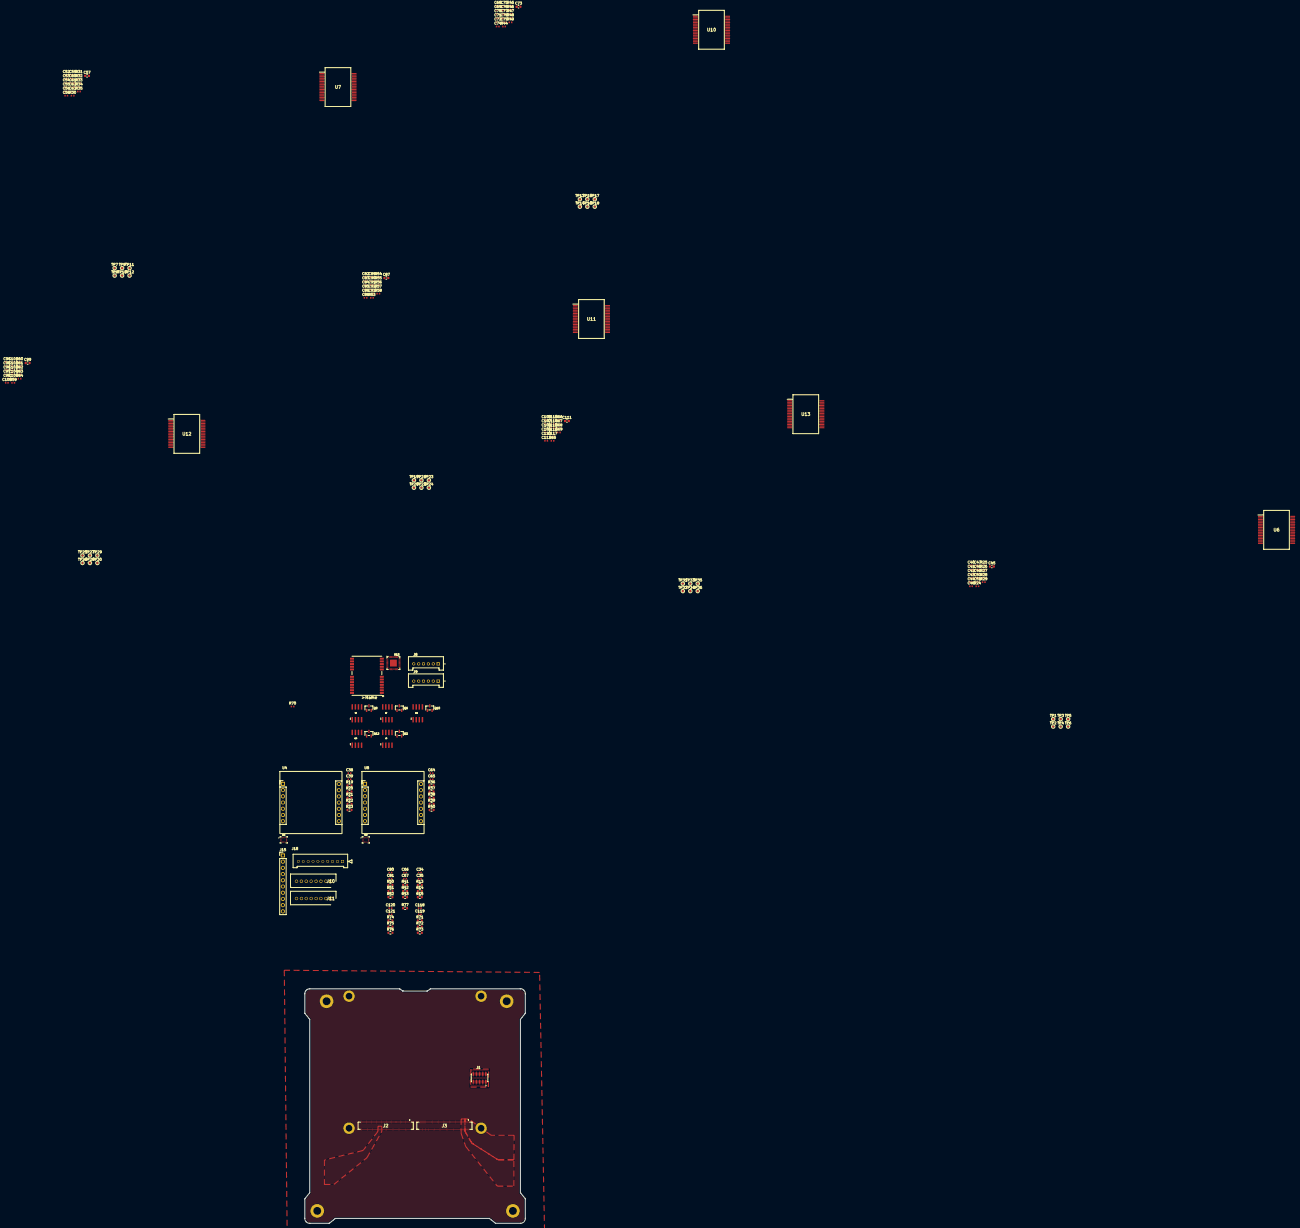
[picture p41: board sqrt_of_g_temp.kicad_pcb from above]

Board: 4 copper layers, 90.2 x 95.9 mm, 223 parts (0 on the bottom side), 128 nets, no tracks yet.

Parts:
C34, C66, C80, C118, C120: 10nF; Perfect_0402
C35, C67, C81, C119, C121: 4.7uF; Perfect_0402
C38, C39, C48, C50, C51, C60, C62, C63, C64, C65, C76, C78, C79, C90, C92, C93, C102, C104, C105, C114, C116, C117: 0.1uF; Perfect_0402
C40, C41, C42, C44, C46, C47, C49, C52, C53, C54, C56, C58, C59, C61, C68, C69, C70, C72, C74, C75, C77, C82, C83, C84, C86, C88, C89, C91, C94, C95, C96, C98, C100, C101, C103, C106, C107, C108, C110, C112, C113, C115: 100nF; Perfect_0402
C43, C55, C71, C85, C97, C109: 1uF; Perfect_0402
C45, C57, C73, C87, C99, C111: 47uF; C_0603_1608Metric
H1, H2, H3, H4: MountingHole_Pad; MountingHole_2.7mm_M2.5_DIN965_Pad
H5, H6, H7, H8: MountingHole_Pad; MountingHole_3.2mm_M3_DIN965_Pad
J1: CLP-105-02-X-D; SAMTEC_CLP-105-02-X-D
J2, J3: DF40HC_3.0_-100DS-0.4V_51_; DF40HC30100DS04V51
J8, J9: 353620650; MOLEX_35362-0650
J10, J11: 353620850; SHDR8W50P0X200_1X8_1830X550X850P
J15: Conn_01x10; PinHeader_1x10_P2.54mm_Vertical
J18: Thruster Connector; CON_353621050
Q2, Q6, Q8, Q10, Q12: IRLML2803; SOT-23
Q3, Q7, Q9, Q11, Q13: NDS8434
R13, R41, R50, R71, R74, R77: 10K; R_0603_1608Metric
R14, R42, R51, R72, R75: 4.7K; R_0603_1608Metric
R15, R43, R52, R73, R76: 3.3k; R_0603_1608Metric
R19, R20, R21, R22, R23, R36, R37, R38, R39, R40: 10k; R_0603_1608Metric
R24, R27, R28, R29, R30, R33, R34, R35, R44, R47, R48, R49, R53, R56, R57, R58, R59, R62, R63, R64, R65, R68, R69, R70: 10k; Perfect_0402
R25, R31, R45, R54, R60, R66: 36k; Perfect_0402
R26, R32, R46, R55, R61, R67: 1; Perfect_0402
TP1, TP2, TP3, TP4, TP5, TP6, TP7, TP8, TP9, TP10, TP11, TP12, TP13, TP14, TP15, TP16, TP17, TP18, TP19, TP20, TP21, TP22, TP23, TP24, TP25, TP26, TP27, TP28, TP29, TP30, TP31, TP32, TP33, TP34, TP35, TP36: TestPoint; TestPoint_Pad_D1.0mm
U4, U8: RM3100 Dev Board; RM3100
U5, U9: BMI270; XDCR_BMI270
U6, U7, U10, U11, U12, U13: DRV8332DKDR; SOP65P1420X360-36N
U14: Orion B16; S1216_24PIN_PACKAGE
U15: EP2W+; QFN32-5X5MM

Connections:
+3V3: J15.1, Q3.1 (Source), Q3.2 (Source), Q3.3 (Source), Q7.1 (Source), Q7.2 (Source), Q7.3 (Source), Q9.1 (Source), Q9.2 (Source), Q9.3 (Source), Q11.1 (Source), Q11.2 (Source), Q11.3 (Source), Q13.1 (Source), Q13.2 (Source), Q13.3 (Source), R15.1, R43.1, R52.1, R73.1, R76.1
+12V: C43.2, C45.2, C46.1, C47.1, C48.1, C49.1, C50.1, C51.1, C55.2, C57.2, C58.1, C59.1, C60.1, C61.1, C62.1, C63.1, C71.2, C73.2, C74.1, C75.1, C76.1, C77.1, C78.1, C79.1, C85.2, C87.2, C88.1, C89.1, C90.1, C91.1, C92.1, C93.1, C97.2, C99.2, C100.1, C101.1, C102.1, C103.1, C104.1, C105.1, C109.2, C111.2, C112.1, C113.1, C114.1, C115.1, C116.1, C117.1, U6.1 (GVDD_B), U6.18 (GVDD_C), U6.19 (GVDD_C), U6.21 (PVDD_C), U6.29 (PVDD_B), U6.34 (PVDD_A), U6.36 (GVDD_A), U7.1 (GVDD_B), U7.18 (GVDD_C), U7.19 (GVDD_C), U7.21 (PVDD_C), U7.29 (PVDD_B), U7.34 (PVDD_A), U7.36 (GVDD_A), U10.1 (GVDD_B), U10.18 (GVDD_C), U10.19 (GVDD_C), U10.21 (PVDD_C), U10.29 (PVDD_B), U10.34 (PVDD_A), U10.36 (GVDD_A), U11.1 (GVDD_B), U11.18 (GVDD_C), U11.19 (GVDD_C), U11.21 (PVDD_C), U11.29 (PVDD_B), U11.34 (PVDD_A), U11.36 (GVDD_A), U12.1 (GVDD_B), U12.18 (GVDD_C), U12.19 (GVDD_C), U12.21 (PVDD_C), U12.29 (PVDD_B), U12.34 (PVDD_A), U12.36 (GVDD_A), U13.1 (GVDD_B), U13.18 (GVDD_C), U13.19 (GVDD_C), U13.21 (PVDD_C), U13.29 (PVDD_B), U13.34 (PVDD_A), U13.36 (GVDD_A)
/3V3_PD1: C80.1, C81.1, J9.1, J11.1, J11.5, Q9.5 (Drain), Q9.6 (Drain), Q9.7 (Drain), Q9.8 (Drain)
/3V3_PD2: C66.1, C67.1, J8.1, J10.1, J10.5, Q7.5 (Drain), Q7.6 (Drain), Q7.7 (Drain), Q7.8 (Drain)
/GPS/3V3_GPS: C118.1, C119.1, Q11.5 (Drain), Q11.6 (Drain), Q11.7 (Drain), Q11.8 (Drain), R77.2, U14.22 (V_BCKP), U14.23 (VCC)
/GPS/EN_GPS: R71.1, R72.1
/GPS/RF_IN: U14.11 (RF_IN), U15.4 (SUM_PORT)
/IMU1_and_MAG1/3V3_SENSORS: C38.1, C39.1, C120.1, C121.1, Q13.5 (Drain), Q13.6 (Drain), Q13.7 (Drain), Q13.8 (Drain), R21.2, R22.1, R23.1, U4.12 (DVDD), U4.13 (AVDD), U5.5 (VDDIO), U5.8 (VDD), U5.10 (OSCB)
/IMU1_and_MAG1/EN_SENSORS: R74.1, R75.1
/IMU2_and_MAG2/3V3_SENSORS: C34.1, C35.1, C64.1, C65.1, Q3.5 (Drain), Q3.6 (Drain), Q3.7 (Drain), Q3.8 (Drain), R38.2, R39.1, R40.1, U8.12 (DVDD), U8.13 (AVDD), U9.5 (VDDIO), U9.8 (VDD), U9.10 (OSCB)
/IMU2_and_MAG2/EN_SENSORS: R13.1, R14.1
/Magnetorquer Controller 1/AGND: C106.1, R66.1, R67.2, U13.9 (AGND), U13.12 (M2)
/Magnetorquer Controller 1/M1: R65.2, U13.13 (M1)
/Magnetorquer Controller 1/OUT_A: C107.1, U13.33 (OUT_A)
/Magnetorquer Controller 1/OUT_B: C108.1, U13.30 (OUT_B)
/Magnetorquer Controller 1/OUT_C: C110.1, U13.22 (OUT_C)
/Magnetorquer Controller 2/AGND: C40.1, R25.1, R26.2, U6.9 (AGND), U6.12 (M2)
/Magnetorquer Controller 2/M1: R24.2, U6.13 (M1)
/Magnetorquer Controller 2/OUT_A: C41.1, U6.33 (OUT_A)
/Magnetorquer Controller 2/OUT_B: C42.1, U6.30 (OUT_B)
/Magnetorquer Controller 2/OUT_C: C44.1, U6.22 (OUT_C)
/Motor Controller 1/AGND: C82.1, R54.1, R55.2, U11.9 (AGND), U11.12 (M2)
/Motor Controller 1/M1: R53.2, U11.13 (M1)
/Motor Controller 1/OUT_A: C83.1, U11.33 (OUT_A)
/Motor Controller 1/OUT_B: C84.1, U11.30 (OUT_B)
/Motor Controller 1/OUT_C: C86.1, U11.22 (OUT_C)
/Motor Controller 2/AGND: C52.1, R31.1, R32.2, U7.9 (AGND), U7.12 (M2)
/Motor Controller 2/M1: R30.2, U7.13 (M1)
/Motor Controller 2/OUT_A: C53.1, U7.33 (OUT_A)
/Motor Controller 2/OUT_B: C54.1, U7.30 (OUT_B)
/Motor Controller 2/OUT_C: C56.1, U7.22 (OUT_C)
/Motor Controller 3/AGND: C94.1, R60.1, R61.2, U12.9 (AGND), U12.12 (M2)
/Motor Controller 3/M1: R59.2, U12.13 (M1)
/Motor Controller 3/OUT_A: C95.1, U12.33 (OUT_A)
/Motor Controller 3/OUT_B: C96.1, U12.30 (OUT_B)
/Motor Controller 3/OUT_C: C98.1, U12.22 (OUT_C)
/Motor Controller 4/AGND: C68.1, R45.1, R46.2, U10.9 (AGND), U10.12 (M2)
/Motor Controller 4/M1: R44.2, U10.13 (M1)
/Motor Controller 4/OUT_A: C69.1, U10.33 (OUT_A)
/Motor Controller 4/OUT_B: C70.1, U10.30 (OUT_B)
/Motor Controller 4/OUT_C: C72.1, U10.22 (OUT_C)
/Photodiode Enable 1/EN: R50.1, R51.1
/Photodiode Enable 2/EN: R41.1, R42.1
/SCL2: R22.2, U4.1 (SCK/SCL), U5.13 (SCX)
/SCL4: R39.2, U8.1 (SCK/SCL), U9.13 (SCX)
/SDA2: R23.2, U4.3 (SI/SDA), U5.14 (SDX)
/SDA4: R40.2, U8.3 (SI/SDA), U9.14 (SDX)
GND: C38.2, C39.2, C46.2, C47.2, C48.2, C49.2, C50.2, C51.2, C58.2, C59.2, C60.2, C61.2, C62.2, C63.2, C64.2, C65.2, C74.2, C75.2, C76.2, C77.2, C78.2, C79.2, C88.2, C89.2, C90.2, C91.2, C92.2, C93.2, C100.2, C101.2, C102.2, C103.2, C104.2, C105.2, C112.2, C113.2, C114.2, C115.2, C116.2, C117.2, H1.1, H2.1, H3.1, H4.1, H5.1, H6.1, H7.1, H8.1, J2.9, J2.10, J2.19, J2.24, J2.29, J2.36, J2.39, J2.49, J2.50, J2.58, J2.59, J2.68, J2.69, J2.78, J2.79, J2.88, J2.89, J2.99, J2.100, J3.18, J3.27, J3.32, J3.39, J3.46, J3.51, J3.60, J3.63, J3.72, J3.75, J3.84, J3.89, J3.90, J3.91, J3.93, J3.95, J3.96, J3.97, J3.99, J8.2, J9.2, J10.2, J10.6, J11.2, J11.6, J15.10, J18.1, J18.10, Q2.2 (S), Q6.2 (S), Q8.2 (S), Q10.2 (S), Q12.2 (S), R13.2, R19.1, R20.1, R24.1, R26.1, R27.1, R28.1, R29.1, R30.1, R32.1, R33.1, R34.1, R35.1, R36.1, R37.1, R41.2, R44.1, R46.1, R47.1, R48.1, R49.1, R50.2, R53.1, R55.1, R56.1, R57.1, R58.1, R59.1, R61.1, R62.1, R63.1, R64.1, R65.1, R67.1, R68.1, R69.1, R70.1, R71.2, R74.2, TP2.1, TP4.1, TP6.1, TP8.1, TP10.1, TP12.1, TP14.1, TP16.1, TP18.1, TP20.1, TP22.1, TP24.1, TP26.1, TP28.1, TP30.1, TP32.1, TP34.1, TP36.1, U4.7 (AVSS), U4.14 (DVSS), U5.1 (SDO), U5.6 (GNDIO), U5.7 (GND), U6.8 (GND), U6.24 (GND), U6.25 (GND), U7.8 (GND), U7.24 (GND), U7.25 (GND), U8.7 (AVSS), U8.14 (DVSS), U9.1 (SDO), U9.6 (GNDIO), U9.7 (GND), U10.8 (GND), U10.24 (GND), U10.25 (GND), U11.8 (GND), U11.24 (GND), U11.25 (GND), U12.8 (GND), U12.24 (GND), U12.25 (GND), U13.8 (GND), U13.24 (GND), U13.25 (GND), U14.10 (GND@10), U14.12 (GND@12), U14.13 (GND@13), U14.24 (GND@24), U15.1 (GND), U15.2 (GND), U15.3 (GND), U15.5 (GND), U15.6 (GND), U15.7 (GND), U15.8 (GND), U15.9 (GND), U15.10 (GND), U15.11 (GND), U15.12 (GND), U15.13 (GND), U15.14 (GND), U15.16 (GND), U15.17 (GND), U15.18 (GND), U15.19 (GND), U15.20 (GND), U15.21 (GND), U15.22 (GND), U15.23 (GND), U15.24 (GND), U15.25 (GND), U15.27 (GND), U15.28 (GND), U15.29 (GND), U15.30 (GND), U15.31 (GND), U15.32 (GND), U15.EP (GND)
unnamed: C34.2, C35.2
unnamed: C66.2, C67.2
unnamed: C80.2, C81.2
unnamed: C118.2, C119.2
unnamed: C120.2, C121.2
unnamed: Q2.3 (D), Q3.4 (Gate), R15.2
unnamed: Q2.1 (G), R14.2
unnamed: Q6.3 (D), Q7.4 (Gate), R43.2
unnamed: Q6.1 (G), R42.2
unnamed: Q8.3 (D), Q9.4 (Gate), R52.2
unnamed: Q8.1 (G), R51.2
unnamed: Q10.3 (D), Q11.4 (Gate), R73.2
unnamed: Q10.1 (G), R72.2
unnamed: Q12.3 (D), Q13.4 (Gate), R76.2
unnamed: Q12.1 (G), R75.2
unnamed: R21.1, U4.10 (I2CEN)
unnamed: R19.2, U4.2 (SO/ADDR1)
unnamed: R20.2, U4.4 (SSN/ADDR0)
unnamed: C41.2, U6.35 (BST_A)
unnamed: C42.2, U6.28 (BST_B)
unnamed: C44.2, U6.20 (BST_C)
unnamed: R29.2, TP5.1, U6.32 (GND_A)
unnamed: R28.2, TP3.1, U6.31 (GND_B)
unnamed: R27.2, TP1.1, U6.23 (GND_C)
unnamed: R25.2, U6.7 (OC_ADJ)
unnamed: C43.1, C45.1, U6.17 (VDD)
unnamed: C40.2, U6.10 (VREG)
unnamed: C53.2, U7.35 (BST_A)
unnamed: C54.2, U7.28 (BST_B)
unnamed: C56.2, U7.20 (BST_C)
unnamed: R35.2, TP11.1, U7.32 (GND_A)
unnamed: R34.2, TP9.1, U7.31 (GND_B)
unnamed: R33.2, TP7.1, U7.23 (GND_C)
unnamed: R31.2, U7.7 (OC_ADJ)
unnamed: C55.1, C57.1, U7.17 (VDD)
unnamed: C52.2, U7.10 (VREG)
unnamed: R38.1, U8.10 (I2CEN)
unnamed: R36.2, U8.2 (SO/ADDR1)
unnamed: R37.2, U8.4 (SSN/ADDR0)
unnamed: C69.2, U10.35 (BST_A)
unnamed: C70.2, U10.28 (BST_B)
unnamed: C72.2, U10.20 (BST_C)
unnamed: R49.2, TP17.1, U10.32 (GND_A)
unnamed: R48.2, TP15.1, U10.31 (GND_B)
unnamed: R47.2, TP13.1, U10.23 (GND_C)
unnamed: R45.2, U10.7 (OC_ADJ)
unnamed: C71.1, C73.1, U10.17 (VDD)
unnamed: C68.2, U10.10 (VREG)
unnamed: C83.2, U11.35 (BST_A)
unnamed: C84.2, U11.28 (BST_B)
unnamed: C86.2, U11.20 (BST_C)
unnamed: R58.2, TP23.1, U11.32 (GND_A)
unnamed: R57.2, TP21.1, U11.31 (GND_B)
unnamed: R56.2, TP19.1, U11.23 (GND_C)
unnamed: R54.2, U11.7 (OC_ADJ)
unnamed: C85.1, C87.1, U11.17 (VDD)
unnamed: C82.2, U11.10 (VREG)
unnamed: C95.2, U12.35 (BST_A)
unnamed: C96.2, U12.28 (BST_B)
unnamed: C98.2, U12.20 (BST_C)
unnamed: R64.2, TP29.1, U12.32 (GND_A)
unnamed: R63.2, TP27.1, U12.31 (GND_B)
unnamed: R62.2, TP25.1, U12.23 (GND_C)
unnamed: R60.2, U12.7 (OC_ADJ)
unnamed: C97.1, C99.1, U12.17 (VDD)
unnamed: C94.2, U12.10 (VREG)
unnamed: C107.2, U13.35 (BST_A)
unnamed: C108.2, U13.28 (BST_B)
unnamed: C110.2, U13.20 (BST_C)
unnamed: R70.2, TP35.1, U13.32 (GND_A)
unnamed: R69.2, TP33.1, U13.31 (GND_B)
unnamed: R68.2, TP31.1, U13.23 (GND_C)
unnamed: R66.2, U13.7 (OC_ADJ)
unnamed: C109.1, C111.1, U13.17 (VDD)
unnamed: C106.2, U13.10 (VREG)
unnamed: R77.1, U14.8 (RSTN)
VDD_1V8: J3.9, J3.10, J3.11, J3.12, J3.13, J3.14, J3.15, J3.16
VDD_3V3: J2.2, J2.4, J2.6, J2.8, J3.1, J3.2, J3.3, J3.4, J3.5, J3.6, J3.7, J3.8
VDD_3V3_LP: J2.60, J2.62, J2.64, J2.66
VSYS: J1.01, J1.02, J1.03, J1.04, J1.05, J1.06, J1.07, J1.08, J1.09, J1.10

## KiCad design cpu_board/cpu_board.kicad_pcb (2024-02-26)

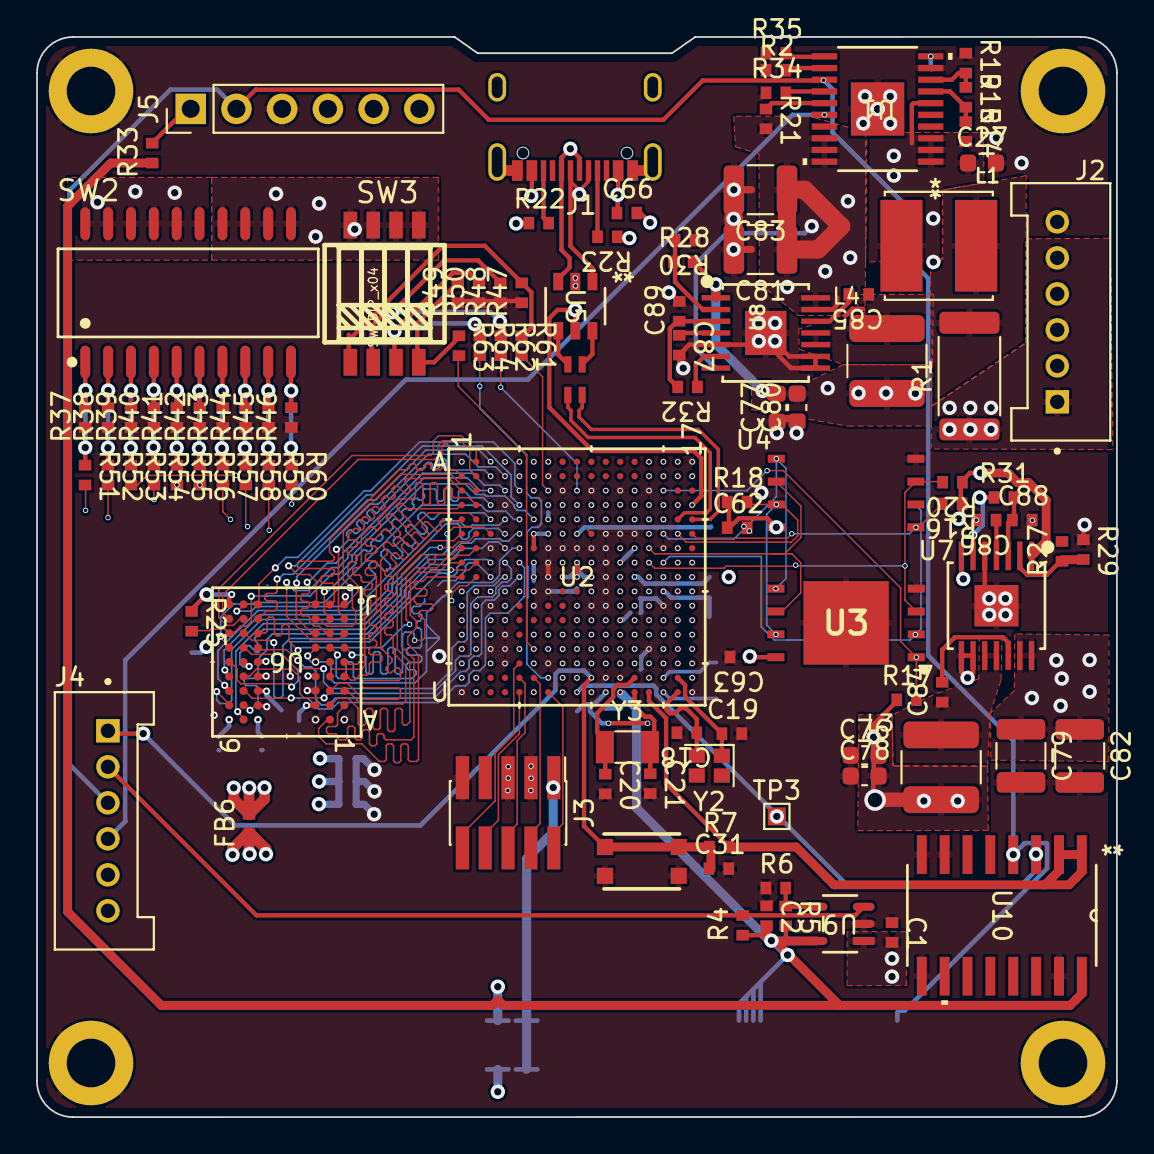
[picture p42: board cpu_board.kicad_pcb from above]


Board: 6 copper layers, 60.0 x 60.0 mm, 169 parts (60 on the bottom side), 252 nets.

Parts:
C1, C2, C60, C62, C63, C88, C89: 1uF; Perfect_0402
C3, C12, C13, C38, C41, C56, C58, C59, C61: 1uF; Perfect_0201
C4, C27, C67, C76, C77, C78, C80: 22uF; C_0603_1608Metric
C5: 10pF; Perfect_0201
C6, C9, C15, C17, C22, C23, C43, C44, C51, C52: 4.7uF; Perfect_0201
C8, C26, C40, C45, C46, C47, C48, C49, C50, C53, C54: 2.2uF; Perfect_0201
C10, C25, C34, C42, C69, C70, C71, C72, C73, C74, C75: 0.1uF; Perfect_0201
C11: 22nF; Perfect_0402
C14: 0.22uF; Perfect_0201
C18, C19: 8pF; Perfect_0402
C20, C21: 10pF; Perfect_0402
C31, C84, C85: 0.1uF; Perfect_0402
C66, C68: 4.7uF; Perfect_0402
C79, C81, C82, C83: 100uF; C_1210_3225Metric
C86, C87: 3.3nF; Perfect_0402
FB1, FB2, FB3, FB6: 190mΩ; Perfect_0402
H1, H2, H3, H4: MountingHole_Pad; MountingHole_2.7mm_M2.5_DIN965_Pad
J1: USB_C_pycubed; USB_C_Receptacle_XKB_U262-161N-4BVC11
J2, J4: 353620650; MOLEX_35362-0650
J3: JTAG_SWD_10; PinHeader_2x05_P1.27mm_Vertical_SMD
J5: Conn_01x06; PinHeader_1x06_P2.54mm_Vertical
J6, J7: DF40C-100DP-0.4V(51); DF40C100DP04V51
L1: 330uH; IND_SRN6045TA-331K
L2: DLW21HN900SQ2L; IND4_CHOKE_0805
L3, L4: 3.3uH; L_2141
R1: 10mΩ; R_2512_6332Metric
R2, R26: 0Ω; Perfect_0402
R3: 10kΩ; Perfect_0201
R4, R7, R16, R17, R21, R33: 10kΩ; Perfect_0402
R5: 2.2MΩ; Perfect_0402
R6: 1.27MΩ; Perfect_0402
R8, R15, R19, R24, R31, R32, R49, R50: 100kΩ; Perfect_0402
R10, R63, R64: 4.7kΩ; Perfect_0402
R14: 800kΩ; Perfect_0402
R18, R20: 33k; Perfect_0402
R22, R23: 5.1kΩ; Perfect_0402
R25: 4.7K - DNP; Perfect_0402
R27: 30.1kΩ; Perfect_0402
R28: 73.2kΩ; Perfect_0402
R29, R30: 22.1kΩ; Perfect_0402
R34: 30kΩ; Perfect_0402
R35: 18kΩ; Perfect_0402
R37, R38, R39, R40, R41, R42, R43, R44, R45, R46, R47, R48: 47kΩ; Perfect_0402
R51, R52, R53, R54, R55, R56, R57, R58, R59, R60, R61, R62: 22kΩ; Perfect_0402
SW1: SWITCH_SMT4.6X2.8; BTN_KMR2_4.6X2.8
SW2: SW_DIP_x10; SW-SMD_DSHP10TS-S
SW3: SW_DIP_x04; SW-SMD_8P-L6.7-W5.4-P1.27-LS8.5
TP1, TP2, TP3: TestPoint; TestPoint_Pad_1.0x1.0mm
U1: TPS16630PWPR; HTSSOP20_PWP_TEX
U2: MIMXRT1176; U_MIMXRT1176DVMAA_NXP
U3: EM064LXQADG13IS1T; SON127P800X600X95-9N-D
U4: MT29F1G01ABBFDWB; UDFN800X600X65-8
U5: USBLC6-2SC6; SOT23-6L_STM
U6: MT48H32M16LFB4-6; VFBGA54_8X8_MRN
U7, U8: TPS54226PWPRPWP14_2P31X2P46-L; PWP14_2P31X2P46-L
U9: LT3014IS5-TRMPBF; S_5_ADI
U10: CD40109BQNSRQ1; NS16
Y2: 24.0mHz; Crystal_SMD_2016-4Pin_2.0x1.6mm
Y3: 32.768kHz; Crystal_SMD_3215-2Pin_3.2x1.5mm

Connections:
/RT1176 #1/CLK1_N: TP2.1, U2.T15 (CLK1_N)
/RT1176 #1/CLK1_P: TP1.1, U2.U15 (CLK1_P)
/RT1176 #1/VDDA_ADC_3P3: C41.1, C42.1, FB1.1, U2.J13 (VDDA_ADC_3P3)
/RT1176 #1/VDD_LPSR_ANA: C15.1, U2.P12 (VDD_LPSR_ANA)
/RT1176 #1/VDD_LPSR_DIG: C23.1, U2.P11 (VDD_LPSR_DIG)
/RT1176 #3/MCM_3V3: C61.1, U2.D16 (USB2_VBUS)
/RT1176 #3/SEMC_DQS: C5.1, U2.J2 (GPIO_EMC_B1_39)
/RT1176 #3/VDD_MIPI_1P0: R3.2, U2.F10 (VDD_MIPI_1P0)
/SDRAM/SDRAM_1V8: C67.1, C68.1, C69.1, C70.1, C71.1, C72.1, C73.1, C74.1, C75.1, FB6.2, R25.1, U6.A7 (VDDQ), U6.A9 (VDD), U6.B3 (VDDQ), U6.C7 (VDDQ), U6.D3 (VDDQ), U6.E7 (VDD), U6.J9 (VDD)
/SDRAM/SEMC_CLK_R: R26.2, U6.F2 (CLK)
/USB-C/USB_CON_DN: J1.A7 (D-), J1.B7 (D-), U5.1 (IO_1_IN)
/USB-C/USB_CON_DP: J1.A6 (D+), J1.B6 (D+), U5.3 (IO_2_IN)
ADC_1V8_IN: C38.1, C40.1, C43.1, FB2.2, U2.G16 (ADC_VREFH), U2.K15 (VDDA_ADC_1P8)
BT_CFG_IO_EN: J6.37, U2.P13 (GPIO_AD_05)
CAMERA_TRIG: J7.81, U2.T2 (GPIO_EMC_B2_17)
DAC_OUT: J6.20, U2.H16 (DAC_OUT)
ENET_RGMII_MDC: J7.85, U2.U2 (GPIO_EMC_B2_19)
ENET_RGMII_MDIO: J7.87, U2.R3 (GPIO_EMC_B2_20)
ENET_RGMII_RXC: J7.22, U2.D13 (GPIO_DISP_B1_01)
ENET_RGMII_RXD0: J7.24, U2.D11 (GPIO_DISP_B1_02)
ENET_RGMII_RXD1: J7.26, U2.E11 (GPIO_DISP_B1_03)
ENET_RGMII_RXD2: J7.28, U2.E10 (GPIO_DISP_B1_04)
ENET_RGMII_RXD3: J7.30, U2.C11 (GPIO_DISP_B1_05)
ENET_RGMII_RX_EN: J7.20, U2.E13 (GPIO_DISP_B1_00)
ENET_RGMII_TXC_BT: J7.44, R56.2, U2.A14 (GPIO_DISP_B1_11)
ENET_RGMII_TXD0_BT: J7.40, R54.2, U2.C13 (GPIO_DISP_B1_09)
ENET_RGMII_TXD1_BT: J7.38, R53.2, U2.A15 (GPIO_DISP_B1_08)
ENET_RGMII_TXD2_BT: J7.36, R52.2, U2.E12 (GPIO_DISP_B1_07)
ENET_RGMII_TXD3_BT: J7.34, R51.2, U2.D10 (GPIO_DISP_B1_06)
ENET_RGMII_TX_EN_BT: J7.42, R55.2, U2.B14 (GPIO_DISP_B1_10)
EN_ADCS: J4.3, J5.2, J6.22, U1.13 (*SHDN), U10.4 (E)
EN_LP: J4.2, R4.2, U9.3 (*SHDN)
FlexSPI_A_CLK: U2.G14 (GPIO_SD_B2_07), U3.6 (CK), U4.6 (SCK)
FlexSPI_A_D0: U2.F15 (GPIO_SD_B2_08), U3.5 (IO0), U4.5 (SI/IO0)
FlexSPI_A_D1: U2.H15 (GPIO_SD_B2_09), U3.2 (IO1), U4.2 (SO/IO1)
FlexSPI_A_D2: R20.2, U2.H14 (GPIO_SD_B2_10), U3.3 (WP#/IO2), U4.3 (WP#/IO2)
FlexSPI_A_D3: R18.2, U2.F16 (GPIO_SD_B2_11), U3.7 (IO3/RESET#), U4.7 (HOLD#/IO3)
FlexSPI_A_SS0: R16.2, U2.F17 (GPIO_SD_B2_06), U4.1 (CS#)
FlexSPI_A_SS1: R17.2, U2.C15 (GPIO_SD_B1_02), U3.1 (CS#)
GND: C1.1, C2.1, C3.1, C4.2, C5.2, C6.2, C8.2, C9.2, C10.2, C11.1, C12.2, C13.2, C14.2, C15.2, C17.2, C18.2, C19.2, C20.2, C21.2, C22.2, C23.2, C25.2, C26.2, C27.2, C31.2, C34.2, C38.2, C40.2, C41.2, C42.2, C43.2, C44.2, C45.2, C46.2, C47.2, C48.2, C49.2, C50.2, C51.2, C52.2, C53.2, C54.2, C56.2, C58.2, C59.2, C60.2, C61.2, C62.2, C63.2, C67.2, C68.2, C69.2, C70.2, C71.2, C72.2, C73.2, C74.2, C75.2, C76.1, C77.1, C78.1, C79.2, C80.1, C81.2, C82.2, C83.2, C86.2, C87.2, C88.2, C89.2, H1.1, H2.1, H3.1, H4.1, J2.2, J2.4, J2.6, J3.3 (GND), J3.5 (GND), J3.9 (GNDDetect), J5.3, J6.9, J6.10, J6.19, J6.24, J6.29, J6.36, J6.39, J6.49, J6.50, J6.58, J6.59, J6.68, J6.69, J6.78, J6.79, J6.88, J6.89, J6.99, J6.100, J6.MH1, J6.MH2, J6.MH3, J6.MH4, J7.18, J7.27, J7.32, J7.39, J7.46, J7.51, J7.60, J7.63, J7.72, J7.75, J7.84, J7.89, J7.90, J7.91, J7.93, J7.95, J7.96, J7.97, J7.99, J7.MH1, J7.MH2, J7.MH3, J7.MH4, R2.1, R3.1, R6.1, R10.1, R19.1, R24.2, R29.1, R30.1, R34.1, R35.1, R37.1, R38.1, R39.1, R40.1, R41.1, R42.1, R43.1, R44.1, R45.1, R46.1, R47.1, R48.1, R49.1, R50.1, SW1.B (S), SW1.B' (S1), U1.9 (GND), U1.21 (GND), U2.A1 (VSS_1), U2.A17 (VSS_2), U2.B7 (VSS_3), U2.C8 (VSS_4), U2.C10 (VSS_5), U2.C12 (VSS_6), U2.C14 (VSS_7), U2.D4 (VSS_8), U2.F11 (VSS_9), U2.F12 (VSS_10), U2.F13 (VSS_11), U2.G3 (VSS_12), U2.G7 (VSS_13), U2.G8 (VSS_14), U2.G9 (VSS_15), U2.G10 (VSS_16), U2.G11 (VSS_17), U2.G15 (VSS_18), U2.H7 (VSS_19), U2.H11 (VSS_20), U2.J7 (VSS_21), U2.J11 (VSS_22), U2.K6 (DCDC_GND_1), U2.K7 (DCDC_GND_2), U2.K11 (VSS_23), U2.L3 (VSS_24), U2.L6 (DCDC_GND_3), U2.L10 (VSS_25), U2.L11 (VSS_26), U2.L15 (VSS_27), U2.N4 (DCDC_MODE), U2.P3 (DCDC_PSWITCH), U2.P4 (VSS_28), U2.P14 (VSS_29), U2.R4 (VSS_34), U2.R7 (VSS_30), U2.T11 (TEST_MODE), U2.T12 (VSS_31), U2.U1 (VSS_32), U2.U17 (VSS_33), U3.4 (VSS), U3.9 (EP), U4.4 (VSS), U5.2 (GND), U6.A1 (VSS), U6.A3 (VSSQ), U6.B7 (VSSQ), U6.C3 (VSSQ), U6.D7 (VSSQ), U6.E3 (VSS), U6.J1 (VSS), U7.5 (GND), U7.8 (PGND1), U7.9 (PGND2), U7.15 (EPAD), U8.5 (GND), U8.8 (PGND1), U8.9 (PGND2), U8.15 (EPAD), U9.2 (GND), U10.7 (ENABLEB), U10.8 (VSS), U10.9 (ENABLEC), U10.15 (ENABLED)
GNDREF: C66.2, J1.A1 (GND), J1.A12 (GND), J1.S1 (SHIELD), J5.4, R22.1, R23.1
GPIO_AD_00: J6.25, U2.N12 (GPIO_AD_00)
GPIO_AD_01: J6.27, U2.R14 (GPIO_AD_01)
GPIO_AD_02: J6.31, U2.R13 (GPIO_AD_02)
GPIO_AD_03: J6.33, U2.P15 (GPIO_AD_03)
GPIO_AD_04: J6.35, U2.M13 (GPIO_AD_04)
GPIO_AD_06: J6.41, U2.N13 (GPIO_AD_06)
GPIO_AD_07: J6.43, U2.T17 (GPIO_AD_07)
GPIO_AD_08: J6.45, U2.R15 (GPIO_AD_08)
GPIO_AD_09: J6.47, U2.R16 (GPIO_AD_09)
GPIO_AD_10: J6.51, U2.R17 (GPIO_AD_10)
GPIO_AD_11: J6.53, U2.P16 (GPIO_AD_11)
GPIO_AD_12: J6.55, U2.P17 (GPIO_AD_12)
GPIO_AD_13: J6.57, U2.L12 (GPIO_AD_13)
GPIO_AD_14: J6.61, U2.N14 (GPIO_AD_14)
GPIO_AD_15: J6.63, U2.M14 (GPIO_AD_15)
GPIO_AD_16: J6.65, U2.N17 (GPIO_AD_16)
GPIO_AD_17: J6.67, U2.N15 (GPIO_AD_17)
GPIO_AD_18: J6.71, U2.M16 (GPIO_AD_18)
GPIO_AD_19: J6.73, U2.L16 (GPIO_AD_19)
GPIO_AD_20: J6.75, U2.K13 (GPIO_AD_20)
GPIO_AD_21: J6.77, U2.K14 (GPIO_AD_21)
GPIO_AD_22: J6.83, U2.K12 (GPIO_AD_22)
GPIO_AD_23: J6.81, U2.J12 (GPIO_AD_23)
GPIO_AD_26: J6.87, U2.L14 (GPIO_AD_26)
GPIO_AD_27: J6.91, U2.N16 (GPIO_AD_27)
GPIO_AD_28: J6.93, U2.L17 (GPIO_AD_28)
GPIO_AD_29: J6.95, U2.M17 (GPIO_AD_29)
GPIO_AD_30: J6.97, U2.K17 (GPIO_AD_30)
GPIO_AD_31: J6.90, U2.J17 (GPIO_AD_31)
GPIO_AD_32: J6.92, U2.K16 (GPIO_AD_32)
GPIO_AD_33: J6.94, U2.H17 (GPIO_AD_33)
GPIO_AD_34: J6.96, U2.J16 (GPIO_AD_34)
GPIO_AD_35: J6.98, U2.G17 (GPIO_AD_35)
GPIO_DISP_B2_00: J7.48, R57.2, U2.E8 (GPIO_DISP_B2_00)
GPIO_DISP_B2_01: J7.50, R58.2, U2.F8 (GPIO_DISP_B2_01)
GPIO_DISP_B2_02: J7.52, R59.2, U2.E9 (GPIO_DISP_B2_02)
GPIO_DISP_B2_03: J7.54, R60.2, U2.D7 (GPIO_DISP_B2_03)
GPIO_DISP_B2_04: J7.56, R61.2, U2.C7 (GPIO_DISP_B2_04)
GPIO_DISP_B2_05: J7.58, R62.2, U2.C9 (GPIO_DISP_B2_05)
GPIO_DISP_B2_06: J7.62, U2.C6 (GPIO_DISP_B2_06)
GPIO_DISP_B2_07: J7.64, U2.D6 (GPIO_DISP_B2_07)
GPIO_DISP_B2_08: J7.66, U2.B5 (GPIO_DISP_B2_08)
GPIO_DISP_B2_09: J7.68, U2.D8 (GPIO_DISP_B2_09)
GPIO_DISP_B2_10: J7.70, U2.D9 (GPIO_DISP_B2_10)
GPIO_DISP_B2_11: J7.74, U2.A6 (GPIO_DISP_B2_11)
GPIO_DISP_B2_12: J7.76, U2.B6 (GPIO_DISP_B2_12)
GPIO_DISP_B2_13: J7.78, U2.A5 (GPIO_DISP_B2_13)
GPIO_DISP_B2_14: J7.80, U2.A7 (GPIO_DISP_B2_14)
GPIO_DISP_B2_15: J7.82, U2.A4 (GPIO_DISP_B2_15)
GPIO_EMC_B1_40: J6.52, U2.K1 (GPIO_EMC_B1_40)
GPIO_EMC_B1_41: J6.54, U2.L1 (GPIO_EMC_B1_41)
GPIO_EMC_B2_00: J7.41, U2.K2 (GPIO_EMC_B2_00)
GPIO_EMC_B2_01: J7.43, U2.K4 (GPIO_EMC_B2_01)
GPIO_EMC_B2_02: J7.45, U2.K3 (GPIO_EMC_B2_02)
GPIO_EMC_B2_03: J7.47, U2.R1 (GPIO_EMC_B2_03)
GPIO_EMC_B2_04: J7.49, U2.M1 (GPIO_EMC_B2_04)
GPIO_EMC_B2_05: J7.53, U2.N1 (GPIO_EMC_B2_05)
GPIO_EMC_B2_06: J7.55, U2.T1 (GPIO_EMC_B2_06)
GPIO_EMC_B2_07: J7.57, U2.M3 (GPIO_EMC_B2_07)
GPIO_EMC_B2_08: J7.59, U2.P1 (GPIO_EMC_B2_08)
GPIO_EMC_B2_09: J7.61, U2.N2 (GPIO_EMC_B2_09)
GPIO_EMC_B2_10: J7.65, U2.R2 (GPIO_EMC_B2_10)
GPIO_EMC_B2_11: J7.67, U2.L4 (GPIO_EMC_B2_11)
GPIO_EMC_B2_12: J7.69, U2.M2 (GPIO_EMC_B2_12)
GPIO_EMC_B2_13: J7.71, U2.K5 (GPIO_EMC_B2_13)
GPIO_EMC_B2_14: J7.73, U2.M4 (GPIO_EMC_B2_14)
GPIO_EMC_B2_15: J7.77, U2.L2 (GPIO_EMC_B2_15)
GPIO_EMC_B2_16: J7.79, U2.P2 (GPIO_EMC_B2_16)
GPIO_EMC_B2_18: J7.83, U2.N3 (GPIO_EMC_B2_18)
GPIO_LPSR_00: J6.1, U2.N6 (GPIO_LPSR_00)
GPIO_LPSR_01: J6.3, U2.R6 (GPIO_LPSR_01)
GPIO_LPSR_02: J6.5, R63.2, U2.P6 (GPIO_LPSR_02)
GPIO_LPSR_03: J6.7, R64.2, U2.T7 (GPIO_LPSR_03)
GPIO_LPSR_04: J6.11, U2.N7 (GPIO_LPSR_04)
GPIO_LPSR_05: J6.13, U2.N8 (GPIO_LPSR_05)
GPIO_LPSR_06: J6.15, U2.P8 (GPIO_LPSR_06)
GPIO_LPSR_07: J6.17, U2.R8 (GPIO_LPSR_07)
GPIO_LPSR_08: J6.21, U2.U8 (GPIO_LPSR_08)
GPIO_LPSR_09: J6.23, U2.P5 (GPIO_LPSR_09)
GPIO_SD_B1_00: J6.26, U2.B16 (GPIO_SD_B1_00)
GPIO_SD_B1_01: J6.28, U2.D15 (GPIO_SD_B1_01)
GPIO_SD_B1_03: J6.30, U2.B17 (GPIO_SD_B1_03)
GPIO_SD_B1_04: J6.32, U2.B15 (GPIO_SD_B1_04)
GPIO_SD_B1_05: J6.34, U2.A16 (GPIO_SD_B1_05)
GPIO_SNVS_00: J7.17, U2.R10 (GPIO_SNVS_00)
GPIO_SNVS_01: J7.19, U2.P10 (GPIO_SNVS_01)
GPIO_SNVS_02: J7.21, U2.L9 (GPIO_SNVS_02)
GPIO_SNVS_03: J7.23, U2.M10 (GPIO_SNVS_03)
GPIO_SNVS_04: J7.25, U2.N10 (GPIO_SNVS_04)
GPIO_SNVS_05: J7.29, U2.P9 (GPIO_SNVS_05)
GPIO_SNVS_06: J7.31, U2.M9 (GPIO_SNVS_06)
GPIO_SNVS_07: J7.33, U2.R9 (GPIO_SNVS_07)
GPIO_SNVS_08: J7.35, U2.N9 (GPIO_SNVS_08)
GPIO_SNVS_09: J7.37, U2.R11 (GPIO_SNVS_09)
JTAG_MOD: R10.2, U2.U6 (GPIO_LPSR_13)
JTAG_TDI: J3.8 (NC/TDI), U2.U5 (GPIO_LPSR_12)
JTAG_TDO: J3.6 (SWO/TDO), U2.T5 (GPIO_LPSR_11)
LPUART1_RX_BOOT: J6.85, U2.M15 (GPIO_AD_25)
unnamed: J5.1, R33.2
unnamed: R37.2, R51.1, SW2.1
unnamed: R38.2, R52.1, SW2.2
unnamed: R39.2, R53.1, SW2.3
unnamed: R40.2, R54.1, SW2.4
unnamed: R41.2, R55.1, SW2.5
unnamed: R42.2, R56.1, SW2.6
unnamed: R43.2, R57.1, SW2.7
unnamed: R44.2, R58.1, SW2.8
unnamed: R45.2, R59.1, SW2.9
unnamed: R46.2, R60.1, SW2.10
unnamed: R47.2, R61.1, SW3.1
unnamed: R48.2, R62.1, SW3.2
unnamed: R49.2, R63.1, SW3.4
unnamed: R50.2, R64.1, SW3.3
unnamed: R21.1, U1.15 (*FLT)
unnamed: C11.2, U1.10 (DVDT)
unnamed: R35.2, U1.11 (ILIM)
unnamed: R34.2, U1.14 (IMON)
unnamed: R2.2, U1.12 (MODE)
unnamed: R15.1, R19.2, U1.8 (OVP)
unnamed: R14.1, R15.2, U1.7 (UVLO)
unnamed: C20.1, U2.T13 (RTC_XTALI), Y3.2
unnamed: C21.1, U2.U13 (RTC_XTALO), Y3.1
unnamed: C34.1, U2.M11 (VDDA_1P8_IN)
unnamed: C18.1, U2.U16 (XTALI), Y2.2
unnamed: C19.1, U2.T16 (XTALO), Y2.1
unnamed: C56.1, FB3.2, U2.F9 (VDD_MIPI_1P8)
unnamed: L2.4, U5.6 (IO_1_OUT)
unnamed: L2.1, U5.4 (IO_2_OUT)
unnamed: R31.1, U7.6 (PG)
unnamed: C86.1, U7.4 (SS)
unnamed: C84.1, L3.1, U7.10 (SW1), U7.11 (SW2)
unnamed: C84.2, U7.12 (VBST)
unnamed: R27.1, R29.2, U7.2 (VFB)
unnamed: C88.1, R31.2, U7.3 (VREG5)
unnamed: R32.1, U8.6 (PG)
unnamed: C87.1, U8.4 (SS)
unnamed: C85.1, L4.1, U8.10 (SW1), U8.11 (SW2)
unnamed: C85.2, U8.12 (VBST)
unnamed: R28.1, R30.2, U8.2 (VFB)
unnamed: C89.1, R32.2, U8.3 (VREG5)
unnamed: R5.1, R6.2, U9.4 (ADJ)
ONOFF: J6.12, U2.U10 (ONOFF)
OTG1_D_N: L2.2, U2.E16 (USB1_DN)
OTG1_D_P: L2.3, U2.E17 (USB1_DP)
PMIC_ON_REQ: J6.18, R8.1, TP3.1, U2.U9 (PMIC_ON_REQ), U10.3 (A)
PMIC_STBY_REQ: J6.14, U2.T9 (PMIC_STBY_REQ)
POR_B: C31.1, J4.1, R7.1, SW1.A, SW1.A' (P1), U2.T10 (~POR)
P_GOOD: J4.4, U1.16 (PGOOD)
SEMC_A0: U2.A3 (GPIO_EMC_B1_09), U6.H7 (A0)
SEMC_A1: U2.A2 (GPIO_EMC_B1_10), U6.H8 (A1)
SEMC_A2: U2.C2 (GPIO_EMC_B1_11), U6.J8 (A2)
SEMC_A3: U2.C5 (GPIO_EMC_B1_12), U6.J7 (A3)
SEMC_A4: U2.D5 (GPIO_EMC_B1_13), U6.J3 (A4)
SEMC_A5: U2.B1 (GPIO_EMC_B1_14), U6.J2 (A5)
SEMC_A6: U2.C1 (GPIO_EMC_B1_15), U6.H3 (A6)
SEMC_A7: U2.D3 (GPIO_EMC_B1_16), U6.H2 (A7)
SEMC_A8: U2.B3 (GPIO_EMC_B1_17), U6.H1 (A8)
SEMC_A9: U2.B4 (GPIO_EMC_B1_18), U6.G3 (A9)
SEMC_A10: U2.B2 (GPIO_EMC_B1_23), U6.H9 (A10)
SEMC_A11: U2.C4 (GPIO_EMC_B1_19), U6.G2 (A11)
SEMC_A12: U2.C3 (GPIO_EMC_B1_20), U6.G1 (A12)
SEMC_BA0: U2.G2 (GPIO_EMC_B1_21), U6.G7 (BA0)
SEMC_BA1: U2.H2 (GPIO_EMC_B1_22), U6.G8 (BA1)
SEMC_CAS: U2.J5 (GPIO_EMC_B1_24), U6.F7 (CAS#)
SEMC_CKE: R24.1, U2.G5 (GPIO_EMC_B1_27), U6.F3 (CKE)
SEMC_CLK: R26.1, U2.J3 (GPIO_EMC_B1_26)
SEMC_CS0: R25.2, U2.E6 (GPIO_EMC_B1_29), U6.G9 (CS#)
SEMC_D0: U2.F3 (GPIO_EMC_B1_00), U6.A8 (DQ0)
SEMC_D1: U2.F2 (GPIO_EMC_B1_01), U6.B9 (DQ1)
SEMC_D2: U2.G4 (GPIO_EMC_B1_02), U6.B8 (DQ2)
SEMC_D3: U2.E4 (GPIO_EMC_B1_03), U6.C9 (DQ3)
SEMC_D4: U2.H5 (GPIO_EMC_B1_04), U6.C8 (DQ4)
SEMC_D5: U2.F4 (GPIO_EMC_B1_05), U6.D9 (DQ5)
SEMC_D6: U2.H4 (GPIO_EMC_B1_06), U6.D8 (DQ6)
SEMC_D7: U2.H3 (GPIO_EMC_B1_07), U6.E9 (DQ7)
SEMC_D8: U2.E3 (GPIO_EMC_B1_30), U6.E1 (DQ8)
SEMC_D9: U2.D2 (GPIO_EMC_B1_31), U6.D2 (DQ9)
SEMC_D10: U2.D1 (GPIO_EMC_B1_32), U6.D1 (DQ10)
SEMC_D11: U2.E2 (GPIO_EMC_B1_33), U6.C2 (DQ11)
SEMC_D12: U2.E1 (GPIO_EMC_B1_34), U6.C1 (DQ12)
SEMC_D13: U2.F1 (GPIO_EMC_B1_35), U6.B2 (DQ13)
SEMC_D14: U2.G1 (GPIO_EMC_B1_36), U6.B1 (DQ14)
SEMC_D15: U2.H1 (GPIO_EMC_B1_37), U6.A2 (DQ15)
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

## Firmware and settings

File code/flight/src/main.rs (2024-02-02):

// ! The starter code slowly blinks the LED, sets up
// ! USB logging, and creates a UART driver using pins
// ! 14 and 15. The UART baud rate is [`UART_BAUD`].
// !
// ! Despite targeting the Teensy 4.0, this starter code
// ! also works on the Teensy 4.1.

#![no_main]
#![no_std]


use teensy4_panic as _;
use teensy4_bsp as bsp;

use bsp::{
    board,
    hal::{timer::Blocking},
};
use embedded_hal::prelude::_embedded_hal_serial_Read;

use bsp::hal::iomuxc;

use tiny_nmea::NMEA;
use heapless::String;

use libgeomag::{GeodeticLocation, ModelExt, WMM, IGRF};

const I2C_PIN_CONFIG: iomuxc::Config = iomuxc::Config::zero()
    .set_open_drain(iomuxc::OpenDrain::Enabled)
    .set_slew_rate(iomuxc::SlewRate::Fast)
    .set_drive_strength(iomuxc::DriveStrength::R0_4)
    .set_speed(iomuxc::Speed::Fast)
    .set_pull_keeper(Some(iomuxc::PullKeeper::Pullup22k));

use teensy4_panic as _;

// use core::fmt::Write as _;

use bsp::hal as hal;
use bsp::ral as ral;
use hal::adc;

// mod Rm3100;
mod constants;
mod rm3100;
mod photodiode;
mod allocator;
mod time;
mod solarsystem_model;
mod linear_algebra;
mod attitude_determination;

use attitude_determination::triad;
use linear_algebra::vec3;
use libm::{sinf, cosf};

/// CHANGE ME to vary the baud rate.
const UART_BAUD: u32 = 9600;
/// Milliseconds to delay before toggling the LED
/// and writing text outputs.
const DELAY_MS: u32 = 50;

#[bsp::rt::entry]
fn main() -> ! {
    // These are peripheral instances. Let the board configure these for us.
    // This function can only be called once!
    let instances = board::instances();

    // This is all the pads on the board
    let pads = unsafe {hal::iomuxc::pads::Pads::new()};

    // Driver resources that are configured by the board. For more information,
    // see the `board` documentation.
    // TODO: refactor into Common and Specifics
    let board::Resources {
        // `pins` has objects that represent the physical pins. The object
        // for pin 13 is `p13`.
        mut pins,
        
        // This is a hardware timer. We'll use it for blocking delays.
        mut gpt1,
        
        // These are low-level USB resources. We'll pass these to a function
        // that sets up USB logging.
        usb,
        
        // This is the GPIO2 port. We need this to configure the LED as a
        // GPIO output.
        mut gpio2,
        
        // This resource is for the UART we're creating.
        lpuart4,

        // I2C
        lpi2c1,
        ..
    } = board::t41(instances);

    // When this returns, you can use the `log` crate to write text
    // over USB. Use either `screen` (macOS, Linux) or PuTTY (Windows)
    // to visualize the messages from this example.
    bsp::LoggingFrontend::default_log().register_usb(usb);

    // configure pull up resistors on the I2C pins
    iomuxc::configure(&mut pins.p18, I2C_PIN_CONFIG);
    iomuxc::configure(&mut pins.p19, I2C_PIN_CONFIG);

    // configure I2C object
    let lpi2c1: board::Lpi2c1 =
        board::lpi2c(lpi2c1, pins.p19, pins.p18, board::Lpi2cClockSpeed::KHz100);

    let lpuart4: board::Lpuart4 =
        board::lpuart(lpuart4, pins.p8, pins.p7, UART_BAUD);

    // let mut rm3100 = RM3100Driver::new(lpi2c1, 0x20);
    let _status_buffer = [0u8; 1]; // Adjust the size of the buffer as needed

    // This configures the LED as a GPIO output.
    let led = board::led(&mut gpio2, pins.p13);

    // Configures the GPT1 timer to run at GPT1_FREQUENCY. See the
    // constants below for more information.
    gpt1.disable();
    gpt1.set_divider(GPT1_DIVIDER);
    gpt1.set_clock_source(GPT1_CLOCK_SOURCE);

    // Convenience for blocking delays.
    let mut delay = Blocking::<_, GPT1_FREQUENCY>::from_gpt(gpt1);

    // Configure the RM3100 magnetometer
    let mut sensor = rm3100::RM3100Driver::new(lpi2c1, 0x20);

    sensor.begin();
    delay.block_ms(250);
    sensor.set_cycle_counts_xyz_equal(200);
    
    // this is the only way I've been able to configure the cycle counts
    // let cc_arr = [0u8, 0u8, 0u8, 0u8, 0u8, 0u8, 200u8, 0u8, 200u8, 0u8, 200u8];
    // sensor.write(rm3100::Register::RM3100_REG_CCX, &cc_arr );
    delay.block_ms(250);
    let mut cc = rm3100::CycleCounts { x: 0, y: 0, z: 0 };
    sensor.get_cycle_counts(&mut cc);
    delay.block_ms(250);
    let mut status_buffer = [0u8; 0x36]; // Adjust the size of the buffer as needed
    sensor.read(rm3100::Register::RM3100_REG_POLL, &mut status_buffer);
    
    sensor.set_rate(100.0);
    delay.block_ms(250);
    sensor.read(rm3100::Register::RM3100_REG_POLL, &mut status_buffer);
    
    sensor.set_continuous_measurement_mode_enabled(true);
    delay.block_ms(250);
    sensor.read(rm3100::Register::RM3100_REG_POLL, &mut status_buffer);

    // Configure the ADC pins.
    let adc1 = unsafe {ral::adc::ADC1::instance() };
    let mut adc1 = adc::Adc::new(adc1, adc::ClockSelect::ADACK, adc::ClockDivision::Div2);
    let mut a0 = adc::AnalogInput::new(pads.gpio_ad_b1.p02);
    let mut a1 = adc::AnalogInput::new(pads.gpio_ad_b1.p03);
    let mut a2 = adc::AnalogInput::new(pads.gpio_ad_b1.p07);
    let mut a3 = adc::AnalogInput::new(pads.gpio_ad_b1.p06);

    let mut counter: u32 = 0;
    
    // test read magnetometer
    
    // log::info!("RM3100 sample: {}, {}, {}", sample.x, sample.y, sample.z);

    let mut nmea = NMEA::new();
    
    let mut string: String<84> = String::new();

    // Add characters to the string
    string.push_str("$GPGGA,161229.487,3723.2475,N,12158.3416,W,1,07,1.0,9.0,M,,,,0000*18\r\n");
    // string.push_str("$GNGLL,4315.68533,N,07955.20234,W,080023.000,A,A*5D\r\n");
    nmea.update(&string);
    // log::info!("longitude: {}", nmea.longitude.unwrap());
    // log::info!("latitude: {}", nmea.latitude.unwrap());
    // log::info!("altitude: {}", nmea.altitude.unwrap());
    // log::info!("time: {:?}", nmea.utc.unwrap());

    // test converting time to julian date
    let date = time::Date {
        day: 17,
        month: 1,
        year: 2020,
    };
    let time = time::Time {
        hour: 10,
        minute: 45,
        second: 0,
        millisecond: 0,
    };
    let jd = time::utc_to_jd(date, time).unwrap();
    // log::info!("julian date: {}", jd);
    // log::info!("sun position: {}, {}, {}", sun_pos_model.x, sun_pos_model.y, sun_pos_model.z);

    // Stanford
    let l = GeodeticLocation::new(37.4277, -122.1701, 0.028956);
    let days_decimal = 2020.0;

    // let wmm = WMM::new(days_decimal).unwrap();
    let igrf = IGRF::new(days_decimal).unwrap();

    // log::info!("created models");
    // let m = wmm.single(l);
    // log::info!("{:?}", m);

    loop {
        led.toggle();
        delay.block_ms(DELAY_MS);
        counter = counter.wrapping_add(1);
        
        // read photodiodes
        let v_z_plus: u16 = adc1.read_blocking(&mut a0);
        let v_y_plus: u16 = adc1.read_blocking(&mut a1);
        let v_z_minus: u16 = adc1.read_blocking(&mut a2);
        let v_y_minus: u16 = adc1.read_blocking(&mut a3);

        log::info!("readings {} {} {} {}", v_z_minus, v_z_plus, v_y_minus, v_y_plus);
        // read magnetometer
        let sample: rm3100::Sample = sensor.get_sample().unwrap();
        let mag_vec_measurement = vec3::new(sample.x as f32, sample.y as f32, sample.z as f32) * 1000.0; // to nT
        // log::info!("mag_vec_measurement: {}, {}, {}", mag_vec_measurement.x, mag_vec_measurement.y, mag_vec_measurement.z);
        let θ: f32 = photodiode::photodiode_pair(v_z_minus, v_z_plus).unwrap() * photodiode::DEGREES_PER_RADIAN;
        let ψ: f32 = photodiode::photodiode_pair(v_y_minus, v_y_plus).unwrap() * photodiode::DEGREES_PER_RADIAN;
        let sun_vec_measurement = vec3::new(
            sinf(ψ)*sinf(θ), 
            cosf(ψ), 
            sinf(ψ)*cosf(θ)
        );
        log::info!("sun_vec_measurement: {}, {}, {}", sun_vec_measurement.x, sun_vec_measurement.y, sun_vec_measurement.z);
        // // read magnetometer
        let sample: rm3100::Sample = sensor.get_sample().unwrap();
        
        let m = igrf.single(l);
        let mag_vec_model = vec3::new(m.x as f32, m.y as f32, m.z as f32);

        let sun_pos_model: vec3 = solarsystem_model::sun_position(jd).unwrap();

        // test triad
        let res = triad(sun_pos_model, mag_vec_model, sun_vec_measurement, mag_vec_model);
        log::info!("Triad test {:?}", res);
        // log::info!("RM3100 sample: {}, {}, {}", sample.x, sample.y, sample.z);
    }
}

// We're responsible for configuring our timers.
// This example uses PERCLK_CLK as the GPT1 clock source,
// and it configures a 1 KHz GPT1 frequency by computing a
// GPT1 divider.
use bsp::hal::gpt::ClockSource;

/// The intended GPT1 frequency (Hz).
const GPT1_FREQUENCY: u32 = 1_000;
/// Given this clock source...
const GPT1_CLOCK_SOURCE: ClockSource = ClockSource::HighFrequencyReferenceClock;
/// ... the root clock is PERCLK_CLK. To configure a GPT1 frequency,
/// we need a divider of...
const GPT1_DIVIDER: u32 = board::PERCLK_FREQUENCY / GPT1_FREQUENCY;

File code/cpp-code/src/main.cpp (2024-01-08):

#include <Arduino.h>
#include <Wire.h>
#include "Rm3100.hpp"
#include <TinyGPS.h>

#define HWSERIAL Serial2

char buf[128];
int addr = 0x20; //((Rm3100::RM3100_ADDR | Rm3100::RM3100_ADDR_SSN) << 1);
struct Rm3100::Status status = { 0 };
struct Rm3100::Sample sample = { 0 };

Rm3100 sensor(Wire, addr);

void setup() {
  // put your setup code here, to run once:
  Serial.begin(115200);
  
  sensor.Begin();
  delay(250);

  sensor.SetCycleCounts(200);
  delay(250);

  sensor.SetRate(100.0f);
  delay(250);

  sensor.SetContinuousMeasurementMode(true);
  delay(250);

}

// Mag Sensor Loop
void loop()
{
    sensor.GetStatus(&status);
    if (status.drdy) {
        sensor.GetSample(&sample);
        
        sprintf(buf, "x: %f, y: %f, z: %f\r\n", sample.x, sample.y, sample.z);
        Serial.print(buf);
    }
    delay(250);
}

//-—————————————————————————————————————————————————————————————————————————————————————————————————————————————————————
//-—————————————————————————————————————————————————————————————————————————————————————————————————————————————————————

// // Photodiode Setup
// int read_sfh2400(uint8_t pin) {
//   int val;
//   val = analogRead(pin);
//   return val;
// }

// // Photodiode Loop
// void loop() {
//   // put your main code here, to run repeatedly:
//   int val0 = read_sfh2400(A0);
//   int val1 = read_sfh2400(A1);
//   int val2 = read_sfh2400(A2);
//   int val3 = read_sfh2400(A3);
//   Serial.print("analog readings: " + String(val0) + "  " + String(val1) + "  " + String(val2) + "  " + String(val3) + "\r\n");
//   delay(250);
// }

//-—————————————————————————————————————————————————————————————————————————————————————————————————————————————————————
//-—————————————————————————————————————————————————————————————————————————————————————————————————————————————————————

// // GPS Setup
// TinyGPS gps;
// void setup()
// {
//   Serial.begin(115200);
//   HWSERIAL.begin(9600);
  
//   Serial.print("Simple TinyGPS library v. "); Serial.println(TinyGPS::library_version());
//   Serial.println("by Mikal Hart");
//   Serial.println();
// }

// // GPS loop
// void loop()
// {
//   bool newData = false;
//   unsigned long chars;
//   unsigned short sentences, failed;

//   // For one second we parse GPS data and report some key values
//   for (unsigned long start = millis(); millis() - start < 1000;)
//   {
//     while (HWSERIAL.available())
//     {
//       char c = HWSERIAL.read();
//       Serial.write(c); // uncomment this line if you want to see the GPS data flowing

//       if (gps.encode(c)) // Did a new valid sentence come in?
//         newData = true;
//     }
//   }

//   if (newData)
//   {
//     float flat, flon;
//     unsigned long age;
//     gps.f_get_position(&flat, &flon, &age);
//     Serial.print("LAT=");
//     Serial.print(flat == TinyGPS::GPS_INVALID_F_ANGLE ? 0.0 : flat, 6);
//     Serial.print(" LON=");
//     Serial.print(flon == TinyGPS::GPS_INVALID_F_ANGLE ? 0.0 : flon, 6);
//     Serial.print(" SAT=");
//     Serial.print(gps.satellites() == TinyGPS::GPS_INVALID_SATELLITES ? 0 : gps.satellites());
//     Serial.print(" PREC=");
//     Serial.print(gps.hdop() == TinyGPS::GPS_INVALID_HDOP ? 0 : gps.hdop());
//   }
  
//   gps.stats(&chars, &sentences, &failed);
//   Serial.print(" CHARS=");
//   Serial.print(chars);
//   Serial.print(" SENTENCES=");
//   Serial.print(sentences);
//   Serial.print(" CSUM ERR=");
//   Serial.println(failed);
//   if (chars == 0)
//     Serial.println("** No characters received from GPS: check wiring **");
// }

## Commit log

2023-10-06 add rough schematic
    [adcs-hardware.kicad_pcb, adcs-hardware.kicad_sch, connectors.kicad_sch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]
2023-10-10 schematic update
    [connectors.kicad_sch, memory_and_storage.kicad_sch, microcontroller.kicad_sch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]
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2023-10-10 update schematic
    [adcs-hardware.kicad_sch, connectors.kicad_sch, microcontroller.kicad_sch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]
2023-10-20 ready for review
    [adcs-hardware.kicad_sch, memory_and_storage.kicad_sch, microcontroller.kicad_sch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]
2023-10-20 add gnd pins
    [adcs-hardware.kicad_sch]
2023-10-20 pete feedback
    [adcs-hardware.kicad_sch, microcontroller.kicad_sch, sensors.kicad_sch]
2023-10-25 add pyramidal breakout board
    [sfh2430_breakout.kicad_pcb, sfh2430_breakout.kicad_sch, smol.kicad_sch]
2023-10-25 move mainboard to subdirectory
    [SFH_2430-Z.step, adcs-hardware.kicad_pcb, adcs-hardware.kicad_sch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]
2023-10-25 add math and decals
    [sfh2430_breakout.kicad_pcb, sfh2430_breakout.kicad_sch, smol.kicad_sch]
2023-10-26 ordered sfh2430 breakout rev 0.1
    [SO-14_S_LIT.step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]
2023-10-30 more schematic work... I was supposed to finish this a long time ago
    [353621050.stp, RT1062_Pin_Functions.xlsx, adcs-hardware.kicad_sch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]
2023-11-01 ready for 2nd round of reviews
    [RT1062_Pin_Functions.xlsx, adcs-hardware.kicad_pcb, adcs-hardware.kicad_sch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]
2023-11-01 add notes
    [adcs-hardware.kicad_sch]
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2023-11-07 add models
    [BMI270.step, MIMXRT1062DVJ6B.step]
2023-11-07 update board
    [adcs-hardware.kicad_pcb, adcs-hardware.kicad_sch, gps.kicad_sch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]
2023-11-07 update pin map
    [RT1062_Pin_Functions.xlsx]
2023-11-07 fix RM3100 read bug and remove debug printing
2023-11-23 add pyramid stl
    [pyramid.stl]
2023-11-24 sfh2400 v2 (flex PCB)
    [sfh2430_breakout-B_Cu.gbr, sfh2430_breakout-B_Mask.gbr, sfh2430_breakout-B_Paste.gbr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]
2024-01-01 update gps schematic
    [gps.kicad_sch]
2024-01-01 update main board
    [adcs-hardware.kicad_pcb, adcs-hardware.kicad_sch, imu_and_magnetometer.kicad_sch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]
2024-01-01 remove prod folder
    [sfh2430_breakout_panelized-B_Cu.gbr, sfh2430_breakout_panelized-B_Mask.gbr, sfh2430_breakout_panelized-B_Paste.gbr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]
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2024-01-01 add 3d models
    [2053380006.stp, 35362-0850.stp, CONN_PH1RB-06.step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]
2024-01-01 update pin map, add RT1176 pin map
    [RT1062_Pin_Functions.xlsx, RT1176_Pin_Functions.xlsx]
2024-01-01 add rt1170 datasheet and mag sensor layout guidelines
2024-01-01 add FDSOI rad ref, mag sensor calibration references
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2024-01-08 don't ground enable pin
    [adcs-hardware.kicad_sch]
2024-01-16 ffc/fpc pyramid
    [individual_v2.dxf, sfh2430_breakout.kicad_pcb, sfh2430_breakout.kicad_sch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]
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2024-02-02 update coil control
    [adcs-hardware.kicad_sch, magnetorquer_controller.kicad_sch, motor_controller.kicad_sch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]
2024-02-02 cpu board in progress
    [cpu_board.kicad_pcb, cpu_board.kicad_sch, interface.kicad_sch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]
2024-02-05 b2b done, erc no errors
    [board_to_board.kicad_sch, cpu_board.kicad_sch, interface.kicad_sch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]
2024-02-05 work on sun pyramid
    [sfh2430_breakout.kicad_pcb, sfh2430_breakout.kicad_sch]
2024-02-06 fix most footprints
    [board_to_board.kicad_sch, cpu_board.kicad_pcb, interface.kicad_sch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]
2024-02-06 JLC parts list complete
    [board_to_board.kicad_sch, cpu_board.kicad_pcb, cpu_board.kicad_sch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]
2024-02-06 add boot switches and fix footprints
    [10DIP.step, bom.xlsx, boot_config.kicad_sch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]
2024-02-06 std size for schematic labels, rm passive lbls
    [board_to_board.kicad_sch, boot_config.kicad_sch, cpu_board.kicad_pcb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]
2024-02-06 add todos and clean up labels
    [cpu_board.kicad_sch, rt1176_3.kicad_sch]
2024-02-08 clean up board2board connector and organize TODOs
    [board_to_board.kicad_sch, boot_config.kicad_sch, cpu_board.kicad_pcb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]
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2024-02-20 route most of power distribution
    [board_to_board.kicad_sch, boot_config.kicad_sch, cpu_board.kicad_pcb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]
2024-02-20 clean up pwr slightly
    [board_to_board.kicad_sch, cpu_board.kicad_pcb, rt1176_2.kicad_sch]
2024-02-21 floorplan complete
    [cpu_board.kicad_pcb, interface.kicad_sch, rt1176_1.kicad_sch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]
2024-02-21 add models and power diagram
    [MT29F2G01ABBGDWB-IT_G_TR.stp, TPS7A4501DCQT.stp, U262-161N-4BVC11.stp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]
2024-02-25 continue work on fanout
    [S_5_ADI.step, boot_config.kicad_sch, cpu_board.kicad_pcb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]
2024-02-26 add load switch
    [NS0016A.stp, PWP0020T.stp, board_to_board.kicad_sch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]
2024-02-26 move level shifter to top
    [cpu_board.kicad_pcb, interface.kicad_sch, power.kicad_sch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]
2024-02-27 clean up silkscreen
    [CLP-105-02-F-D.stp, FTS-105-03-F-DV.stp, board_to_board.kicad_sch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]
2024-02-28 soldermander 1.0 ready for review
    [bom.xlsx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]
2024-02-28 PCBranch ready for review
    [PCBranch-B_Cu.gbr, PCBranch-B_Mask.gbr, PCBranch-B_Paste.gbr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]
2024-02-28 rename to Soldermander
    [Soldermander.kicad_sch, board_to_board.kicad_sch, boot_config.kicad_sch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]
2024-02-28 move boards to hardware/
    [10DIP.step, 2053380006.stp, 35362-0850.stp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]
2024-02-29 update 3.3uH inductor
    [DRV8332DKDR.stp, Soldermander.kicad_sch, adcs-hardware.kicad_sch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]
2024-07-26 pre-autorouter part 2
    [Soldermander.kicad_sch, board_to_board.kicad_sch, boot_config.kicad_sch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]
2024-08-06 ads board 1.0.1
    [gps.kicad_sch, imu_and_magnetometer.kicad_sch, lora_2400.kicad_sch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]
2024-08-06 PCB routing and silkscreen
    [PrintedCoralBoard.kicad_pcb]
2024-08-06 add pics
    [PrintedCoralBoard.kicad_pcb]
2024-08-06 fix landing pattern
    [9774030151R.stp, NEO.STEP, PrintedCoralBoard.kicad_pcb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]
2024-08-08 add PiCoral 1.0.0
    [5055670631.stp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]
2024-08-08 update names
    [BOM_JLCSMT.xlsx, BOM_SELF_ASSEMBLY.xlsx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]
